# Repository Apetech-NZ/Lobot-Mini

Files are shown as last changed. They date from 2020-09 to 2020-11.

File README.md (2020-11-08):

# Lobot-Mini
An ESP32-based controller for FRA Antweight (SPARC Fairyweight) robots

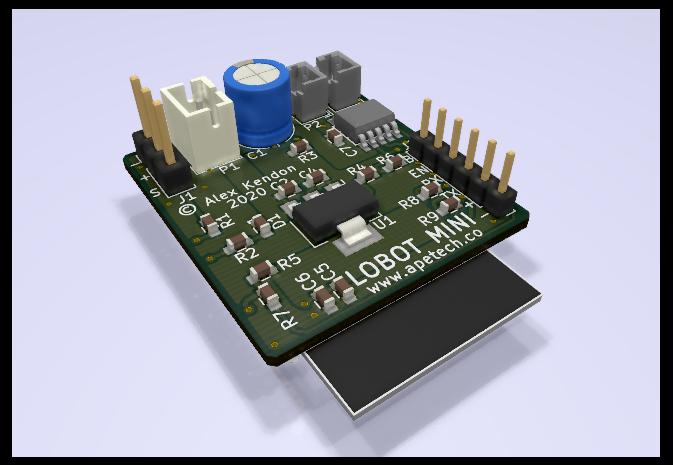
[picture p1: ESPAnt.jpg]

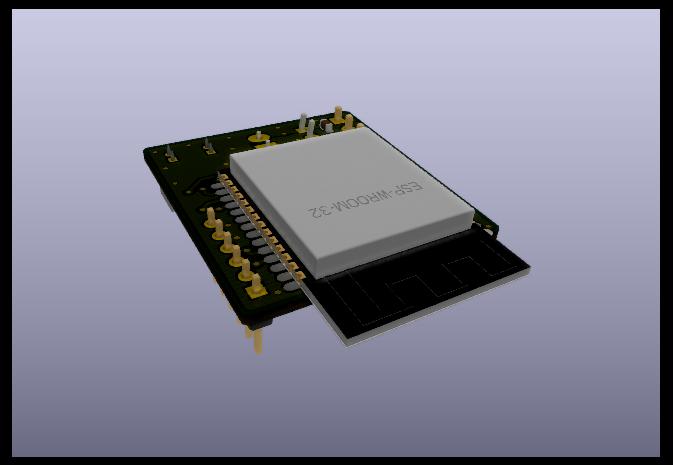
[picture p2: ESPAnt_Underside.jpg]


# NOTE:
**This project is still under heavy development!!!** Everything you need to build your own Lobot-Mini board and control it from and Android device is here, but it is very much in an Alpha/Debug state. If there is enough interest I will continue to develop proper release versions of the firmware and app.

## Background
Over the last couple of years, in my spare time, I've been developing a simple low-cost robot called [Lobot](https://github.com/Apetech-NZ/Lobot). After I got involved in combat robotics I noted that the cost of the hardware, the transmitter in particular, was a barrier for some people. I realised that Lobot actually already had all the necessary functionality to control an Antweight robot, but it is designed as a standalone device with the drive motors, battery etc... mounted directly to the PCB and size optimized for hand-assembly. I stripped out all the unnecessary functionality and shrank the board as much as possible (without increasing the cost of the PCB too much and still allowing for hand-assembly). To keep the cost and size down I've kept the design relatively simple and haven't included much in the way of protection (same as most hobby-grade electronics).

## Features
- Bluetooth communication (Control via BT3, BTLE is available)
- Wifi connectivity (just for firmware updates at this stage)
- Dual H-bridge output for driving N20 or similar brushed motors
- PWM output for a servo or ESC

## Specifications
- Battery Voltage: 4.6~10V (Designed for 2S)
- Motor Current: TBD

## Pinout
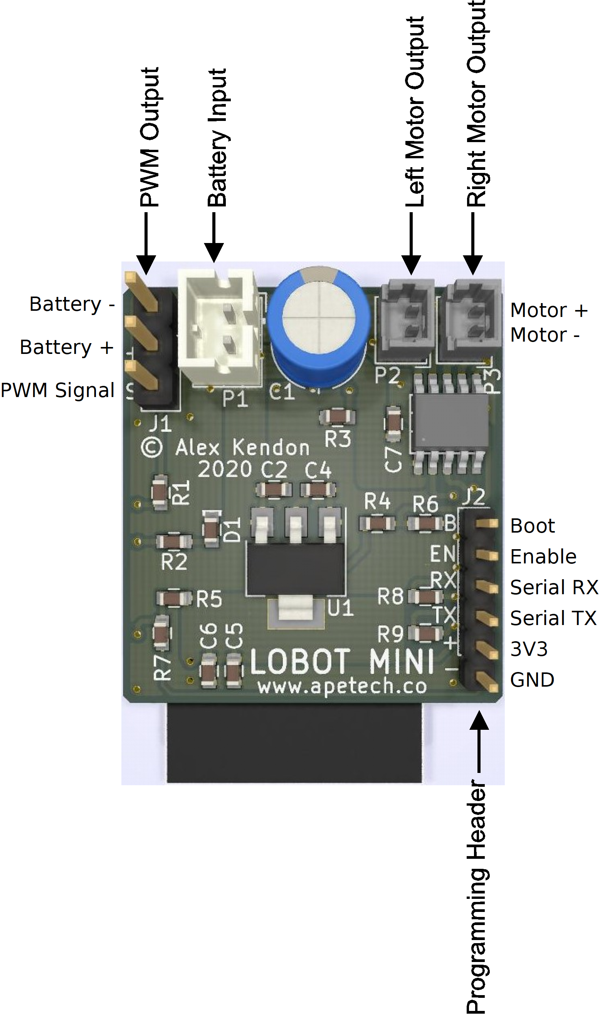
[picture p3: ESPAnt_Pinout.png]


# Building It
If you would like to build a Lobot-Mini board please consider purchasing the PCBs from my project page on [PCB Way](https://www.pcbway.com/project/shareproject/Lobot_Mini.html). I get a small percentage of the PCB purchase price and every cent helps me keep developing Lobot-Mini

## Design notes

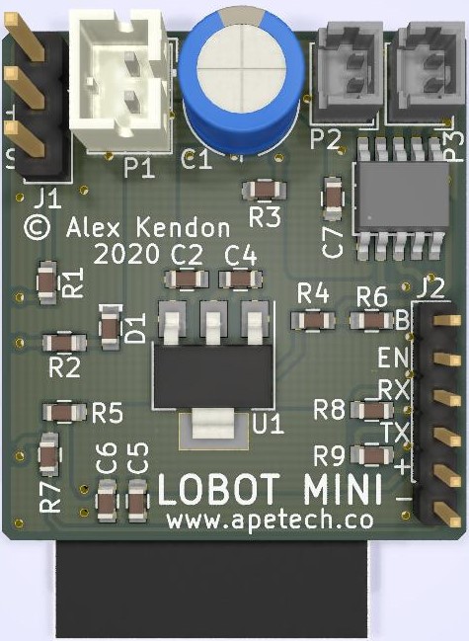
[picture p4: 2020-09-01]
pictures/ESPAnt_top.jpg

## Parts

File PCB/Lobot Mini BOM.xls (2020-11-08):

Lobot Mini / ESPAnt
Reference(s) | Value | LibPart | Mfr 1 | Mfr 1 Part # | Mfr 2 | Mfr 2 Part #
C1 | 220U_16V | C_220U_16V_ElectroPolymer_Radial | Kemet | A750EK227M1CAAE016
C2 | 1U_10V | C_1U_10V_0603_X5R | Samsung | LMK107BBJ106MALT | MuRata | GRM188R61A105KA61D
C3 | 1U_10V | C_1U_10V_0603_X5R | Samsung | LMK107BBJ106MALT | MuRata | GRM188R61A105KA61D
C4 | 10U_10V | C_10U_10V_0603_X5R | Taiyo Yuden | LMK107BBJ106MALT | MuRata | GRM188R61A106ME69D
C5 | 10U_10V | C_10U_10V_0603_X5R | Taiyo Yuden | LMK107BBJ106MALT | MuRata | GRM188R61A106ME69D
C6 | 100N_50V | C_100N_50V_0603_X7R | Yageo | CC0603JRX7R9BB104
C7 | 1U_10V | C_1U_10V_0603_X5R | Samsung | LMK107BBJ106MALT | MuRata | GRM188R61A105KA61D
D1 | BLU | D_LED_BLU_0603 | Wurth | 150060BS75000 | Lite-On | LTST-C194TBKT
J1 | Conn_01x03 | Conn_01x03
J2 | 2mm Header 6way | Conn_01x06
P1 | PH_2WAY | J_PH_Header_LOCK_2WAY_2mm_R_A | JST | S2B-PH-K-S(LF)(SN)
P2 | MOTOR_CONN_01X02 | CONN_01X02 | TE | 640456-2
P3 | MOTOR_CONN_01X02 | CONN_01X02 | TE | 640456-2
R1 | 33R | R_33R_1PC_100PPM_0603 | Yageo | RC0603FR-0733RL
R2 | 470R | R_470R_1PC_100PPM_0603 | Yageo | RC0603FR-07470RL | Vishay | CRCW0603470RFKEAHP
R3 | 1K | R_1K_1PC_100PPM_0603 | Yageo | RC0603FR-071KL
R4 | 10K | R_10K_1PC_100PPM_0603 | Yageo | RC0603FR-0710KL
R5 | 10K | R_10K_1PC_100PPM_0603 | Yageo | RC0603FR-0710KL
R6 | 0R | R_0R_1PC_100PPM_0603 | Yageo | RC0603FR-070RL
R7 | 0R | R_0R_1PC_100PPM_0603 | Yageo | RC0603FR-070RL
R8 | 33R | R_33R_1PC_100PPM_0603 | Yageo | RC0603FR-0733RL
R9 | 33R | R_33R_1PC_100PPM_0603 | Yageo | RC0603FR-0733RL
U1 | 3V3_1A | U_IC_LDO_3V3_1A_SOT223 | Diodes Inc | AZ1117EH-3.3TRG1 | On Semiconductor | NCP1117ST33T3G
U2 | ESP32-WROOM-32 | U_RFMod_ESP32-WROOM-32 | Espressif Systems | ESP32-WROOM-32
U3 | LV8548MC | U_IC_LV8548MC_DUAL_H_BRIDGE | On Semi | LV8548MC-AH

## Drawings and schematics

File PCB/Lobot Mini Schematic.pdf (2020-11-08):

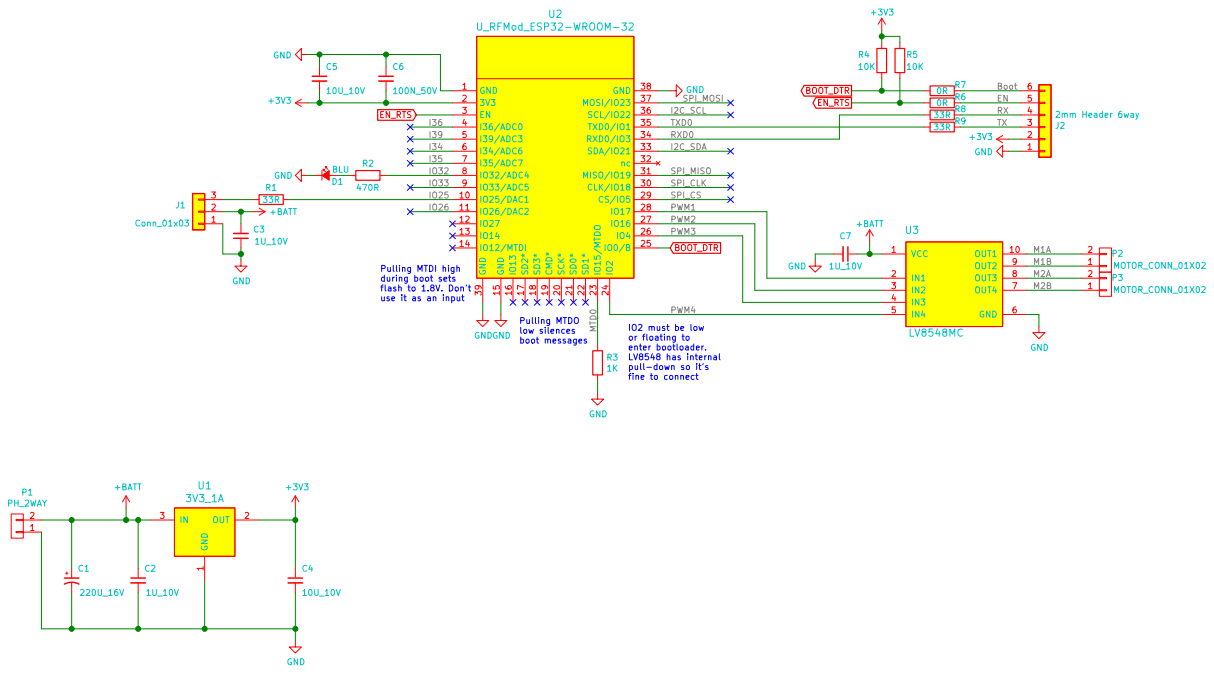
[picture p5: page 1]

Pulling MTDI high
during boot sets
flash to 1.8V. Don't use it as an input

fine to connect Pulling MTDO
low silences boot messages

IO2 must be low
or floating to
enter bootloader. LV8548 has internal pull-down so it's

Id: 1/1 Title: Low Lobot File: ESPAnt.sch Sheet: /

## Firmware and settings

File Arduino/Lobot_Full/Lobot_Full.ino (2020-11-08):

#include <WiFi.h>
#include <ESPmDNS.h>
#include <WiFiUdp.h>
#include <ArduinoOTA.h>
#include <WiFiClient.h>
#include <WebServer.h>
#include <Update.h>

#include "Lobot_Internal_EEPROM.h"

#define SOFTWARE_VERSION  "0.1"

//#define DEBUG_DRIVE_MOTORS

//For Tasks
TaskHandle_t LEDTask;

//For Internal EEPROM
LobotEEPROM lobot_eeprom;

//For Sleep mode
#define uS_TO_S_FACTOR 1000000
#define uS_TO_mS_FACTOR 1000

//For Bluetooth
#define BLUETOOTH_NAME "Lobot"
#define BLUETOOTH_PIN "lobot"
#include "BluetoothSerial.h"
#if !defined(CONFIG_BT_ENABLED) || !defined(CONFIG_BLUEDROID_ENABLED)
#error Bluetooth is not enabled! Please run `make menuconfig` to and enable it
#endif
BluetoothSerial SerialBT;

//For WiFi
#define WIFI_MAX_CONNECT_ATTEMPTS 2
#define HOSTNAME  "Lobot"
WebServer server(80);
bool wifi_connected = false;

//For command line interface
#define WIFI_SSID_COMMAND "ssid"

#define WIFI_KEY_COMMAND "key"

#define DATA_RATE_COMMAND "dataperiod"

#define DEVICE_ADDRESS_MAX 1000
#define DEVICE_ADDRESS_COMMAND "address"

#define WIFI_ENABLED_COMMAND "wifi"
#define WIFI_ENABLED  1
#define WIFI_DISABLED 0

#define RESET_COMMAND "reset"
#define ACK_COMMAND "ahoyhoy"
#define ACK_REPLY "ahoy"
#define IP_COMMAND "ip"
#define VERSION_COMMAND "version"

#define SLEEP_ENABLED_COMMAND "sleep"

#define DRIVE_STOP_COMMAND "s"
#define DRIVE_FORWARD_COMMAND "f"
#define DRIVE_BACKWARD_COMMAND "b"
#define DRIVE_LEFT_COMMAND "l"
#define DRIVE_RIGHT_COMMAND "r"
#define MOTOR_LEFT_COMMAND "ml"
#define MOTOR_RIGHT_COMMAND "mr"

#define ESC_DUTY_COMMAND "esc"

//For Lobot IO
#define LED0_PIN 14 
#define LED1_PIN 12

#define LOBOT_MINI_LED_PIN 32

#define BOOT_PIN 0    //Use the boot pin to disable sleep

#define SUPPLY_MEASURE_PIN  A6

#define PWM1_PIN 17
#define PWM2_PIN 16
#define PWM3_PIN 4
#define PWM4_PIN 2
#define ESC0_PIN 25

#define ESC0_COUNT_MIN      1200
#define ESC0_COUNT_MAX      8600
#define ESC0_INPUT_DUTY_MAX 255

#define WAKE_PIN_BITMASK 0x000000001  //Set the bit positon of the GPIO number

//For Lobot system
//#define HEARTBEAT_RESET_COUNT 100
//#define HEARTBEAT_TIMER_DELAY 120000

uint8_t systemStatus = 0;
//int heartbeat = HEARTBEAT_RESET_COUNT;
uint8_t sleep_en = 0;
int32_t data_delay = 60000;
//uint32_t lastTransmitTime = 0;
//uint32_t lastHeartbeatTime = 0;
uint8_t wifi_enable = 1;
int16_t lobot_address = 0;

//const int flash_delay = 500;
const int comms_timeout_delay = 500;
//int last_time = 0;
int comms_timeout = 0;


void setup() 
{
  uint32_t wifi_attempts = 0;
  String ssid = "empty";
  String key = "empty";

  //Setup GPIO
  pinMode(LED0_PIN,OUTPUT);
  digitalWrite(LED0_PIN,HIGH);
  pinMode(LED1_PIN,OUTPUT);
  digitalWrite(LED1_PIN,HIGH);
  pinMode(LOBOT_MINI_LED_PIN,OUTPUT);
  digitalWrite(LOBOT_MINI_LED_PIN,HIGH);

  pinMode(BOOT_PIN,INPUT_PULLUP);

  ledcSetup(0, 500, 8);
  ledcAttachPin(PWM1_PIN,0);

  ledcSetup(1, 500, 8);
  ledcAttachPin(PWM2_PIN,1);

  ledcSetup(2, 500, 8);
  ledcAttachPin(PWM3_PIN,2);  

  ledcSetup(3, 500, 8);
  ledcAttachPin(PWM4_PIN,3); 

  ledcSetup(4, 50, 16);
  ledcAttachPin(ESC0_PIN,4);
  ledcWrite(4,ESC0_COUNT_MIN); //Immediately set the count for the ESC PWM to try and stop the ESC getting upset

  //Turn the "power" LED on
  digitalWrite(LED0_PIN,true);
 
  Serial.begin(115200,SERIAL_8N1,3,1);  //Force the serial pins to UART0 pins
  Serial.println("Booting");
  

  ////////////////////////////// Bluetooth Setup ///////////////////////////////////
  //Construct the bluetooth identifier
  String bluetooth_id = (String(BLUETOOTH_NAME) + '_' + String(lobot_eeprom.ReadInt(DEVICE_ADDRESS_EEPROM_ADDRESS)));
  String bluetooth_pin = (String(BLUETOOTH_PIN));
  SerialBT.setPin(bluetooth_pin.c_str());
  //SerialBT.enableSSP();
  SerialBT.begin(bluetooth_id.c_str()); //Bluetooth device name
  SerialBT.setTimeout(1000);

  ////////////////////////////// EEPROM Setup ///////////////////////////////////
  //Try to intialise the EEPROM. If it initialises OK read out the system settings
  //if (!EEPROM.begin(EEPROM_SIZE))
  if(!lobot_eeprom.begin())
  {
    Serial.println("failed to initialise EEPROM");
  }
  else
  {
    data_delay = lobot_eeprom.ReadUint32(DATA_RATE_ADDRESS);
    //Since it's an int it could be negative. Just use the absolute value
    lobot_address = abs(lobot_eeprom.ReadInt(DEVICE_ADDRESS_EEPROM_ADDRESS));
    
    //Load the wifi and MQTT credentials from EEPROM
    ssid = lobot_eeprom.ReadString(WIFI_SSID_EEPROM_ADDRESS,WIFI_SSID_EEPROM_LENGTH);
    key = lobot_eeprom.ReadString(WIFI_KEY_EEPROM_ADDRESS,WIFI_KEY_EEPROM_LENGTH);
    wifi_enable = lobot_eeprom.ReadByte(WIFI_ENABLED_EEPROM_ADDRESS);
    sleep_en = lobot_eeprom.ReadByte(SLEEP_ENABLED_EEPROM_ADDRESS);
  }

  ////////////////////////////// Deep Sleep Setup ///////////////////////////////
  //Print the wakeup reason for ESP32
  print_wakeup_reason();

  /*
  First we configure the wake up source
  We set our ESP32 to wake up every <data_delay> milliseconds
  */
  esp_sleep_enable_timer_wakeup(data_delay * uS_TO_mS_FACTOR);
  Serial.println("Setup ESP32 to sleep for every " + String(data_delay/1000) +
  " Seconds");

  //Ext1 can operate in ultra-low power, EXT0 requires the GPIO peripheral to be powered up
  //Only RTC IO can be used as a source for external wake source. They are pins: 0,2,4,12-15,25-27,32-39.
  esp_sleep_enable_ext1_wakeup(WAKE_PIN_BITMASK,ESP_EXT1_WAKEUP_ALL_LOW);


  ////////////////////////////// WIFI SETUP /////////////////////////////////////
  WiFi.mode(WIFI_STA);
  
  while((wifi_attempts < WIFI_MAX_CONNECT_ATTEMPTS) && (wifi_connected != true))
  {
    WiFi.begin(ssid.c_str(), key.c_str());

    if(WiFi.waitForConnectResult() == WL_CONNECTED)
    {
      wifi_connected = true;
    }
    else
    {
      delay(5000);
      Serial.println("WiFi Connection Failed!");
      wifi_connected = false;
    }

    wifi_attempts ++;
  }

  // Port defaults to 3232
  // ArduinoOTA.setPort(3232);

  // Hostname defaults to esp3232-[MAC]
  ArduinoOTA.setHostname("Lobot");

  // No authentication by default
  ArduinoOTA.setPassword("lobot");

  // Password can be set with it's md5 value as well
  // MD5(admin) = 21232f297a57a5a743894a0e4a801fc3
  // ArduinoOTA.setPasswordHash("21232f297a57a5a743894a0e4a801fc3");

  ArduinoOTA
    .onStart([]() {
      String type;
      if (ArduinoOTA.getCommand() == U_FLASH)
        type = "sketch";
      else // U_SPIFFS
        type = "filesystem";

      // NOTE: if updating SPIFFS this would be the place to unmount SPIFFS using SPIFFS.end()
      Serial.println("Start updating " + type);
    })
    .onEnd([]() {
      Serial.println("\nEnd");
    })
    .onProgress([](unsigned int progress, unsigned int total) {
      Serial.printf("Progress: %u%%\r\n", (progress / (total / 100)));
    })
    .onError([](ota_error_t error) {
      Serial.printf("Error[%u]: ", error);
      if (error == OTA_AUTH_ERROR) Serial.println("Auth Failed");
      else if (error == OTA_BEGIN_ERROR) Serial.println("Begin Failed");
      else if (error == OTA_CONNECT_ERROR) Serial.println("Connect Failed");
      else if (error == OTA_RECEIVE_ERROR) Serial.println("Receive Failed");
      else if (error == OTA_END_ERROR) Serial.println("End Failed");
    });

  ArduinoOTA.begin();

  //Create a host name for the web updater
  String host = (String(HOSTNAME) + '_' + String(lobot_eeprom.ReadInt(DEVICE_ADDRESS_EEPROM_ADDRESS)));
  //Start the web updater server
  WebUpdaterBegin(host);

  Serial.print("IP address: ");
  Serial.println(WiFi.localIP());

  Serial.println("Ready");

  //////////////////////////////// Timer Setup ////////////////////////////////////
  //last_time = millis();
  comms_timeout = millis() + comms_timeout_delay;

  Serial.print("setup() finished on core ");
  Serial.println(xPortGetCoreID());

  ///////////////////////////////Create Tasks//////////////////////////////////////
  //TODO: Add different flash states and a queue to set states from different tasks
  xTaskCreatePinnedToCore(
      LEDTaskCode, /* Function to implement the task */
      "LEDTask", /* Name of the task */
      1000,  /* Stack size in words */
      NULL,  /* Task input parameter */
      0,  /* Priority of the task */
      &LEDTask,  /* Task handle. */
      0); /* Core where the task should run */
}


//############################################################ LOOP #################################################################
void loop() 
{
  uint32_t i = 0;
  String cmd_in;
  String arg_in;

  //Check to see if any commands have come in on the serial interfaces
  if(Serial.available() > 0)
  {
    ReceiveSerialCommand();
  }

  if(SerialBT.available() > 0)
  {
    ReceiveSerialBTCommand();
  }

  //If the comms timeout has been exceeded the stop the drive motors and ESC
  if(millis() > comms_timeout)
  {
    DriveStop();
    //esc_channel0.write(0);
  }

  if(wifi_connected == true)
  {
    //Run OTA handlers
    ArduinoOTA.handle();
    server.handleClient();
  }
}

//////////////////////////////////////////////////////////////////////// Motor Control functions /////////////////////////////////////////////////////////////////

void DriveStop(void)
{
  #ifdef DEBUG_DRIVE_MOTORS
  Serial.println("Stop");
  #endif

  digitalWrite(LED0_PIN,LOW);
  digitalWrite(LED1_PIN,LOW);
  
  ledcWrite(0, 0);
  ledcWrite(1, 0); 
  ledcWrite(2, 0);
  ledcWrite(3, 0);  
}

void DriveForward(uint16_t duty)
{
  #ifdef DEBUG_DRIVE_MOTORS
  Serial.print("Forward ");
  Serial.println(duty);
  #endif

  digitalWrite(LED0_PIN,HIGH);
  digitalWrite(LED1_PIN,HIGH);
  
  ledcWrite(0, 0);
  ledcWrite(1, duty); 
  ledcWrite(2, duty);
  ledcWrite(3, 0);  
}

void DriveBackward(uint16_t duty)
{
  #ifdef DEBUG_DRIVE_MOTORS
  Serial.print("Reverse ");
  Serial.println(duty);
  #endif

  digitalWrite(LED0_PIN,LOW);
  digitalWrite(LED1_PIN,LOW);
  
  ledcWrite(0, duty);
  ledcWrite(1, 0); 
  ledcWrite(2, 0);
  ledcWrite(3, duty);  
}

void DriveLeft(uint16_t duty)
{
  #ifdef DEBUG_DRIVE_MOTORS
  Serial.print("Left ");
  Serial.println(duty);
  #endif

  digitalWrite(LED0_PIN,HIGH);
  digitalWrite(LED1_PIN,LOW);
  
  ledcWrite(0, 0);
  ledcWrite(1, duty); 
  ledcWrite(2, 0);
  ledcWrite(3, duty);  
}

void DriveRight(uint16_t duty)
{
  #ifdef DEBUG_DRIVE_MOTORS
  Serial.print("Right ");
  Serial.println(duty);
  #endif

  digitalWrite(LED0_PIN,LOW);
  digitalWrite(LED1_PIN,HIGH);  
  
  ledcWrite(0, duty);
  ledcWrite(1, 0); 
  ledcWrite(2, duty);
  ledcWrite(3, 0);  
}

void MotorLeft(int16_t duty)
{
  #ifdef DEBUG_DRIVE_MOTORS
  Serial.print("Left Motor ");
  Serial.println(duty);
  #endif

  digitalWrite(LED1_PIN,HIGH);  

  if(duty > 0)
  {
    ledcWrite(0, 0);
    ledcWrite(1, abs(duty));
  }
  else if (duty < 0)
  {
    ledcWrite(0, abs(duty));
    ledcWrite(1, 0); 
  }
  else
  {
    ledcWrite(0, 0);
    ledcWrite(1, 0); 
    digitalWrite(LED1_PIN,LOW);
  }

}

void MotorRight(int16_t duty)
{
  #ifdef DEBUG_DRIVE_MOTORS
  Serial.print("Right Motor ");
  Serial.println(duty);
  #endif

  digitalWrite(LED0_PIN,HIGH);
  
 
  if(duty > 0)
  {
    ledcWrite(2, abs(duty));
    ledcWrite(3, 0); 
  }
  else if (duty < 0)
  {
    ledcWrite(2, 0);
    ledcWrite(3, abs(duty));     
  }
  else
  {
    ledcWrite(2, 0);
    ledcWrite(3, 0); 
    digitalWrite(LED0_PIN,LOW);
  }
}

void ESC0_SetDuty(int16_t duty)
{
  //For the ESC we will only accept positive values (since that's how the ESCs work)
  int16_t esc0_duty = abs(duty);
  
  #ifdef DEBUG_DRIVE_MOTORS
  Serial.print("ESC 0 ");
  Serial.println(duty);
  #endif

  //Scale the duty to 255, similar to the drive motors
  esc0_duty = (duty * (ESC0_COUNT_MAX - ESC0_COUNT_MIN))/ESC0_INPUT_DUTY_MAX;
  esc0_duty += ESC0_COUNT_MIN;

  //Apply limits to the count value that will set the PWM. Going outside min/max duty results in the ESC packing a sad
  if(esc0_duty < ESC0_COUNT_MIN) esc0_duty = ESC0_COUNT_MIN;
  else if (esc0_duty > ESC0_COUNT_MAX) esc0_duty = ESC0_COUNT_MAX;

  //Now set the pwm duty
  ledcWrite(4, esc0_duty); 
}

//////////////////////////////////////////////////////////////////////// CLI functions /////////////////////////////////////////////////////////////////
void ReceiveSerialCommand(void)
{
  String cmd_in = Serial.readStringUntil('=');
  String arg_in = Serial.readString();
  
  ParseCommand(cmd_in,arg_in,&Serial);
}

void ReceiveSerialBTCommand(void)
{
  String cmd_in = SerialBT.readStringUntil('=');
  String arg_in = SerialBT.readStringUntil('\r');
  SerialBT.flush();
  
  ParseCommand(cmd_in,arg_in,&SerialBT);
}

void ParseCommand(String cmd_in, String arg_in, Stream *cli_stream)
{
  bool command_valid = true;
    //Serial.print("command received: ");
    //Serial.print(cmd_in);
    //Serial.print(", with argument: ");
    //Serial.println(arg_in);

    if (cmd_in.equalsIgnoreCase(String(WIFI_SSID_COMMAND)))
    {
      ProcessArg(arg_in,String(WIFI_SSID_COMMAND),WIFI_SSID_EEPROM_ADDRESS,WIFI_SSID_EEPROM_LENGTH,true,cli_stream);
    }
    else if (cmd_in.equalsIgnoreCase(String(WIFI_KEY_COMMAND)))
    {
       ProcessArg(arg_in,String(WIFI_KEY_COMMAND),WIFI_KEY_EEPROM_ADDRESS,WIFI_KEY_EEPROM_LENGTH,false,cli_stream);
    } 
    else if (cmd_in.equalsIgnoreCase(String(DATA_RATE_COMMAND)))
    {
       ProcessArgUint32(arg_in,String(DATA_RATE_COMMAND),DATA_RATE_ADDRESS,DATA_RATE_LENGTH,true,cli_stream);
    } 
    else if (cmd_in.equalsIgnoreCase(String(WIFI_ENABLED_COMMAND)))
    {
       ProcessArgByte(arg_in,String(WIFI_ENABLED_COMMAND),WIFI_ENABLED_EEPROM_ADDRESS,true,cli_stream);
    }
    else if (cmd_in.equalsIgnoreCase(String(DEVICE_ADDRESS_COMMAND)))
    {
      ProcessArgInt16(arg_in,String(DEVICE_ADDRESS_COMMAND),DEVICE_ADDRESS_EEPROM_ADDRESS,DEVICE_ADDRESS_EEPROM_LENGTH,true,cli_stream);
    } 
    else if (cmd_in.equalsIgnoreCase(String(SLEEP_ENABLED_COMMAND)))
    {
       ProcessArgByte(arg_in,String(SLEEP_ENABLED_COMMAND),SLEEP_ENABLED_EEPROM_ADDRESS,true,cli_stream);
    }


    else if (cmd_in.equalsIgnoreCase(String(DRIVE_STOP_COMMAND)))
    {
      DriveStop();
    }
    else if (cmd_in.equalsIgnoreCase(String(DRIVE_FORWARD_COMMAND)))
    {
      DriveForward(ArgToUint16(arg_in));
    }
    else if (cmd_in.equalsIgnoreCase(String(DRIVE_BACKWARD_COMMAND)))
    {
      DriveBackward(ArgToUint16(arg_in));
    }
    else if (cmd_in.equalsIgnoreCase(String(DRIVE_LEFT_COMMAND)))
    {
      DriveLeft(ArgToUint16(arg_in));
    }
    else if (cmd_in.equalsIgnoreCase(String(DRIVE_RIGHT_COMMAND)))
    {
      DriveRight(ArgToUint16(arg_in));
    }
    else if (cmd_in.equalsIgnoreCase(String(MOTOR_LEFT_COMMAND)))
    {
      MotorLeft(ArgToInt16(arg_in));
    }
    else if (cmd_in.equalsIgnoreCase(String(MOTOR_RIGHT_COMMAND)))
    {
      MotorRight(ArgToInt16(arg_in));
    }
        else if (cmd_in.equalsIgnoreCase(String(ESC_DUTY_COMMAND)))
    {
      ESC0_SetDuty(ArgToInt16(arg_in));  
    }


    
    else if (cmd_in.equalsIgnoreCase(String(RESET_COMMAND)))
    {
      cli_stream->println("Resetting in 1 second");
      delay(1000);
      ESP.restart();
    }
    else if (cmd_in.equalsIgnoreCase(String(IP_COMMAND)))
    {
      cli_stream->println(String(String(IP_COMMAND) + "=" + (WiFi.localIP().toString())));
    } 
    else if (cmd_in.equalsIgnoreCase(String(VERSION_COMMAND)))
    {
      cli_stream->println(String(String(VERSION_COMMAND) + "=" + String(SOFTWARE_VERSION)));
    } 
    else if(cmd_in.equalsIgnoreCase(String(ACK_COMMAND)))
    {
      cli_stream->println(ACK_REPLY);
    } 
    else
    {
      cli_stream->print("Error: Command = ");
      cli_stream->print(cmd_in);
      cli_stream->print(" Arg = ");
      cli_stream->println(arg_in);
      
      command_valid = false; //Don't update the comms timeout for invalid commands
    }

    //Update the comms timeout if a valid command was received
    if(command_valid == true)
    {
      comms_timeout = millis() + comms_timeout_delay;
    }
  
}



void ProcessArg(String arg_string, String command, int eeprom_address, int eeprom_length, bool read_enable, Stream *cli_stream)
{
      if(IsQuery(arg_string))        //((arg_in.charAt(0) == '?') && ((arg_in.charAt(1) == '\r') || (arg_in.charAt(1) == '\n')))    //(arg_in == String("?"))
      {
        if(read_enable)
        {
          cli_stream->println(String(command + "=" + lobot_eeprom.ReadString(eeprom_address,eeprom_length)));
        }
        else
        {
          cli_stream->println(String(command + "=Private"));
        }
      }
      else if(IsInvalid(arg_string,eeprom_length))     //((arg_in.charAt(0) == '\r') || (arg_in.charAt(0) == '\n') || (arg_in.length() > WIFI_SSID_EEPROM_LENGTH))
      {
        cli_stream->println(String(command + "=invalid"));
      }
      else
      {
        //looks like Serial.readString() is now returning the new line and carrige return characters. Null these out as they screw up the wifi and MQTT setup
        arg_string.replace('\r',0);
        arg_string.replace('\n',0);
        
        lobot_eeprom.WriteString(arg_string,eeprom_address,eeprom_length);
        cli_stream->println(String(command + "=OK"));
      }
}


void ProcessArgInt16(String arg_string, String command, int eeprom_address, int eeprom_length, bool read_enable, Stream *cli_stream)
{
      //looks like Serial.readString() is now returning the new line and carrige return characters. Null these out as they screw up the atoi
      arg_string.replace('\r',0);
      arg_string.replace('\n',0);
      int16_t arg_int = arg_string.toInt();
      
      if(IsQuery(arg_string))        //((arg_in.charAt(0) == '?') && ((arg_in.charAt(1) == '\r') || (arg_in.charAt(1) == '\n')))    //(arg_in == String("?"))
      {
        if(read_enable)
        {
          cli_stream->println(String(command + "=" + String(lobot_eeprom.ReadInt(eeprom_address))));
        }
        else
        {
          cli_stream->println(String(command + "=Private"));
        }
      }
      else if(arg_int > 32767 || arg_int < -32768) //((arg_in.charAt(0) == '\r') || (arg_in.charAt(0) == '\n') || (arg_in.length() > WIFI_SSID_EEPROM_LENGTH))
      {
        cli_stream->println(String(command + "=invalid"));
      }
      else
      {
        lobot_eeprom.WriteInt(arg_int,eeprom_address);
        cli_stream->println(String(command + "=OK"));
      }
}


void ProcessArgUint32(String arg_string, String command, int eeprom_address, int eeprom_length, bool read_enable, Stream *cli_stream)
{
      //looks like Serial.readString() is now returning the new line and carrige return characters. Null these out as they screw up the atoi
      arg_string.replace('\r',0);
      arg_string.replace('\n',0);
      int32_t arg_int = arg_string.toInt();
      
      if(IsQuery(arg_string))        //((arg_in.charAt(0) == '?') && ((arg_in.charAt(1) == '\r') || (arg_in.charAt(1) == '\n')))    //(arg_in == String("?"))
      {
        if(read_enable)
        {
          cli_stream->println(String(command + "=" + String(lobot_eeprom.ReadUint32(eeprom_address))));
        }
        else
        {
          cli_stream->println(String(command + "=Private"));
        }
      }
      else if(arg_int > 4294967295) //((arg_in.charAt(0) == '\r') || (arg_in.charAt(0) == '\n') || (arg_in.length() > WIFI_SSID_EEPROM_LENGTH))
      {
        cli_stream->println(String(command + "=invalid"));
      }
      else
      {
        lobot_eeprom.WriteUint32(arg_int,eeprom_address);
        cli_stream->println(String(command + "=OK"));
      }
}


void ProcessArgByte(String arg_string, String command, int eeprom_address, bool read_enable, Stream *cli_stream)
{
      //looks like Serial.readString() is now returning the new line and carrige return characters. Null these out as they screw up the atoi
      arg_string.replace('\r',0);
      arg_string.replace('\n',0);
      uint8_t arg_byte = arg_string.toInt();
      
      if(IsQuery(arg_string))
      {
        if(read_enable)
        {
          cli_stream->println(String(command + "=" + String(lobot_eeprom.ReadByte(eeprom_address))));
        }
        else
        {
          cli_stream->println(String(command + "=Private"));
        }
      }
      else if(arg_byte > 255 || arg_byte < 0) 
      {
        cli_stream->println(String(command + "=invalid"));
      }
      else
      {
        lobot_eeprom.WriteByte(arg_byte,eeprom_address);
        cli_stream->println(String(command + "=OK"));
      }
}



bool IsQuery(String arg_string)
{
  if((arg_string.charAt(0) == '?') && ((arg_string.charAt(1) == '\r') || (arg_string.charAt(1) == '\n') || (arg_string.charAt(1) == 0)))    //(arg_in == String("?"))
  {
    return true;
  }
  else
  {
    return false;
  }
}

bool IsInvalid(String arg_string, int max_length)
{
  if((arg_string.charAt(0) == '\r') || (arg_string.charAt(0) == '\n') || (arg_string.length() > max_length))
  {
    return true;
  }
  else
  {
    return false;
  }
}

uint16_t ArgToUint16(String arg_string)
{
  //looks like Serial.readString() is now returning the new line and carrige return characters. Null these out as they screw up the atoi
  arg_string.replace('\r',0);
  arg_string.replace('\n',0);
  //There is a possiblity the argument could be negative so read it into an int32 before taking the abs value
  int32_t arg_int = arg_string.toInt();

  //Cap the value of arg_int to 65536 before casting to uint16
  if (arg_int > 0xFFFF) arg_int = 0xFFFF;
  else if (arg_int < -0xFFFF) arg_int = -0xFFFF;

  //Take the absolute value of arg_int as we are casting to uint16
  arg_int = abs(arg_int);

  //Cast to uint16 and return that
  return uint16_t(arg_int);
}

int16_t ArgToInt16(String arg_string)
{
  //looks like Serial.readString() is now returning the new line and carrige return characters. Null these out as they screw up the atoi
  arg_string.replace('\r',0);
  arg_string.replace('\n',0);
  int16_t arg_int = arg_string.toInt();

  return arg_int;
}
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

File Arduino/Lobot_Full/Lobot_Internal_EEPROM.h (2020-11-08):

#ifndef LobotInternalEEPROM_h
#define LobotInternalEEPROM_h

#include <Arduino.h>

//For EEPROM
#include "EEPROM.h"
#define EEPROM_SIZE 1024

#define WIFI_SSID_EEPROM_ADDRESS 32
#define WIFI_SSID_EEPROM_LENGTH 32

#define WIFI_KEY_EEPROM_ADDRESS 64
#define WIFI_KEY_EEPROM_LENGTH 64

#define DATA_RATE_ADDRESS  128
#define DATA_RATE_LENGTH 4

#define DEVICE_ADDRESS_EEPROM_ADDRESS 150
#define DEVICE_ADDRESS_EEPROM_LENGTH 2

#define WIFI_ENABLED_EEPROM_ADDRESS  160
#define WIFI_ENABLED_EEPROM_LENGTH  1

#define MQTT_BROKER_EEPROM_ADDRESS  170
#define MQTT_BROKER_EEPROM_LENGTH   32

#define MQTT_PASS_EEPROM_ADDRESS    210
#define MQTT_PASS_EEPROM_LENGTH     32

#define MQTT_USER_EEPROM_ADDRESS    245
#define MQTT_USER_EEPROM_LENGTH     32

#define SLEEP_ENABLED_EEPROM_ADDRESS  280
#define SLEEP_ENABLED_EEPROM_ADDRESS  1

class LobotEEPROM 
{
    private:
    boolean initialized;
    
    public:
    LobotEEPROM();
    boolean begin(void);
    void WriteString(String data,int dataAddress, int dataLength);
    String ReadString(int dataAddress,int dataLength);
    int ReadInt(int dataAddress);
    void WriteInt(int data,int dataAddress);
    uint32_t ReadUint32(int dataAddress);
    void WriteUint32(uint32_t data, int dataAddress);
    void WriteByte(uint8_t data, int dataAddress);
    uint8_t ReadByte(int dataAddress);
};



#endif //LobotInternalEEPROM_h

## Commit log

2020-09-01 Added some board renders to pictures
2020-11-08 Added Arduino source, PCB details and Android APK
    [Lobot Mini BOM.xls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]
